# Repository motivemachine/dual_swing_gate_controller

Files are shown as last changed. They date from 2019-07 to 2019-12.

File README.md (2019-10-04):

#### Remote linear actuator controller, for a diy open-source gate opener.

Having built a custom driveway gate and hinge setup I found myself shocked at what a quality dual-swing gate opener costs these days. More importantly, they have rather a lack of customization available in how you control or communicate with them, so I've set out to build my own with a pair of 12v linear actuators and a Semtech SX1287 LORA radio module. This is a work in progress.  

I'll be building a custom PCB for the whole thing, but I've tried to design this in such a way that any number of Arduino and related modules would work if hand-wired with jumpers, perfboard, breadboard, etc. Most parts are through-hole, and the ones that are surface mount are large enough hand soldering should be easy. Also makes for easy customization.

##### Current Status
Schematic and first soldered board is complete. Code testing has begun, and has been mostly reliable with a few adjustments needed in error handling functions and long-term robust-ness. 

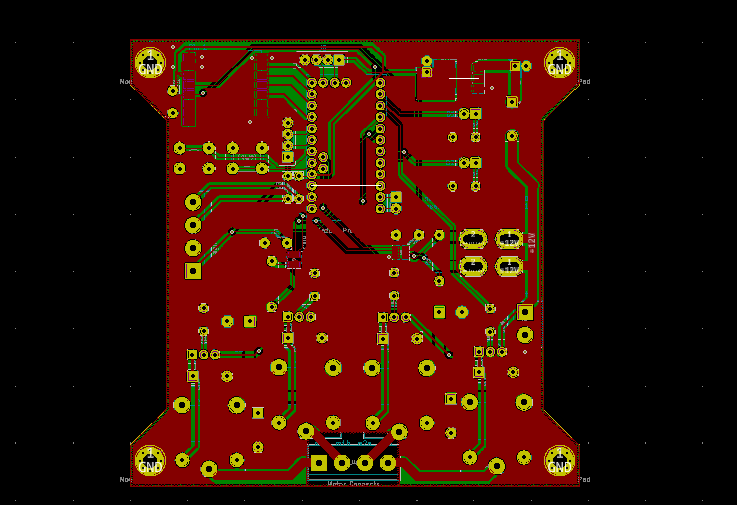
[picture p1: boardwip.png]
gate control board


##### Parts list and design criteria
* **2x 16" stroke linear actuators (12v)** - commercial gate openers are often much larger than this, but so often are the gates larger and heavier. My gates are quite lightweight tubing on ball-bearing hinges, so not much force is needed to open them. The two actuators I have claim a full load current of 3 amps, though I don't expect them to need much more than 1 to open and close these gates
* **2x 8Ah SLA batteries** - the driveway is long enough that trenching AC power out there would be a chore, so I'll be running this off a pair of ~$16 12v batteries and a small solar panel instead.
* **Arduino Pro mini 8Mhz/3.3v** - chosen so that I can avoid level shifting the SPI/I2C modules. An arduino Uno or Nano would work fine with proper level shifting
* **AI-thinker RA-02 Lora** radio - I've come to like these for designs that may be put in varied enclosures, as the IPX connector built-in means I can place the radio anywhere that's convenient and pipe the RF via coax to an optimal antenna placement.
* **4x 12volt SPDT relays** of proper current rating- The relays are in an H-Bridge topology that allows reversing of current through a DC motor(see below). This could be done a little cleaner with a pair of DPDT relays, but using these means the design will also work with the standard 4-place relay modules that are so popular. They are a 12v coil powered off the battery, switched with a PNP from the Atmega328p.
* **2x INA219**- These can be had in SOT23-8 package, or available in several types of breakout boards. These will be the primary safety, which will watch the current going to each actuator. We'll test for a baseline current it usually takes to open a given gate (perhaps in a light breeze) and set that as our upper limit of motor current. If this current is exceeded, it likely means a gate is jammed or attempting to close on an object; so stop and reverse the gate.
  * Most of the pre-built modules I've seen for sale us a 2010 0.1ohm shunt resistor, allowing a maximum current of 3 amps. If your motors draw more than that, recalculate the needed resistor value
  * There will be enough exposed pins to add an electronic-eye, but I haven't planed for that yet.
* **2x mini ATM fuse**- the INA219 will handle over-current due to obstructions in the motor, these are just extra safety in case of a major hardware or wiring failure. Size appropriately to your wire sizes and motor current requirements.
* **AMS1117-3.3 regulator**- For the 3.3v circuitry.
* **A MAG3110 or similar magnetometer**- this is optional, but I've decided to build-in my magnetometer driveway alarm into this same enclosure and power supply. It is described here: [magneto-driveway-alarm](www.gitlab.com/motivemachine/magneto-driveway-alarm)
  * The magnetometer from a more common IMU package (i.e. mpu9250) would likely also work well.

##### H-Bridge description
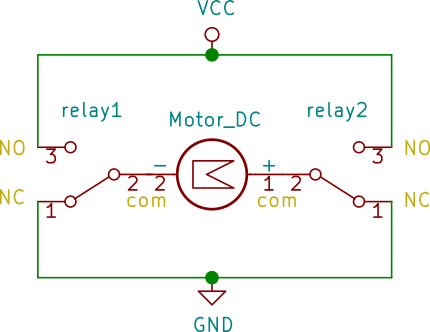
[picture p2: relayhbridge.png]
hbridge schematic
  
Shown here is the relay configuration in a simple H-Bridge. By switching seperate relays, any leg can be made positive, while the other remains grounded, causing the DC motor to be able to turn in two directions. This is very fault tolerant too- if any relay became stuck or failed, the motor would have either both leads grounded, or both leads at 12 volts, neither one of which would allow current to flow, therefore the motor will remain stopped. If the linear actuator is moving, it will of course stop when it reaches the built-in limit switches.
  Avid home DIY'ers might recognize this as similar to wiring a 3-way light switch, but backwards. The other difference is that AC power has no single direction of current flow, nor does a lightbulb care which way the current flows.

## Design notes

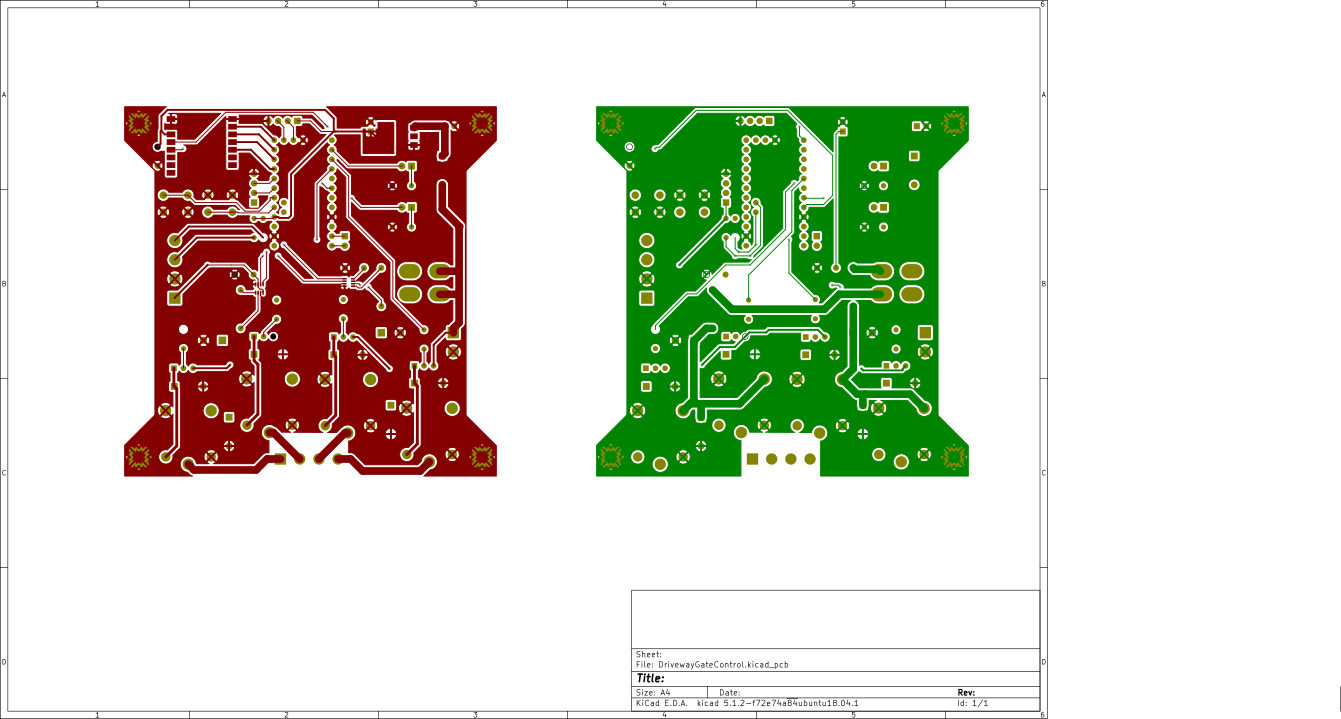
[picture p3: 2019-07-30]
BoardLayers.png

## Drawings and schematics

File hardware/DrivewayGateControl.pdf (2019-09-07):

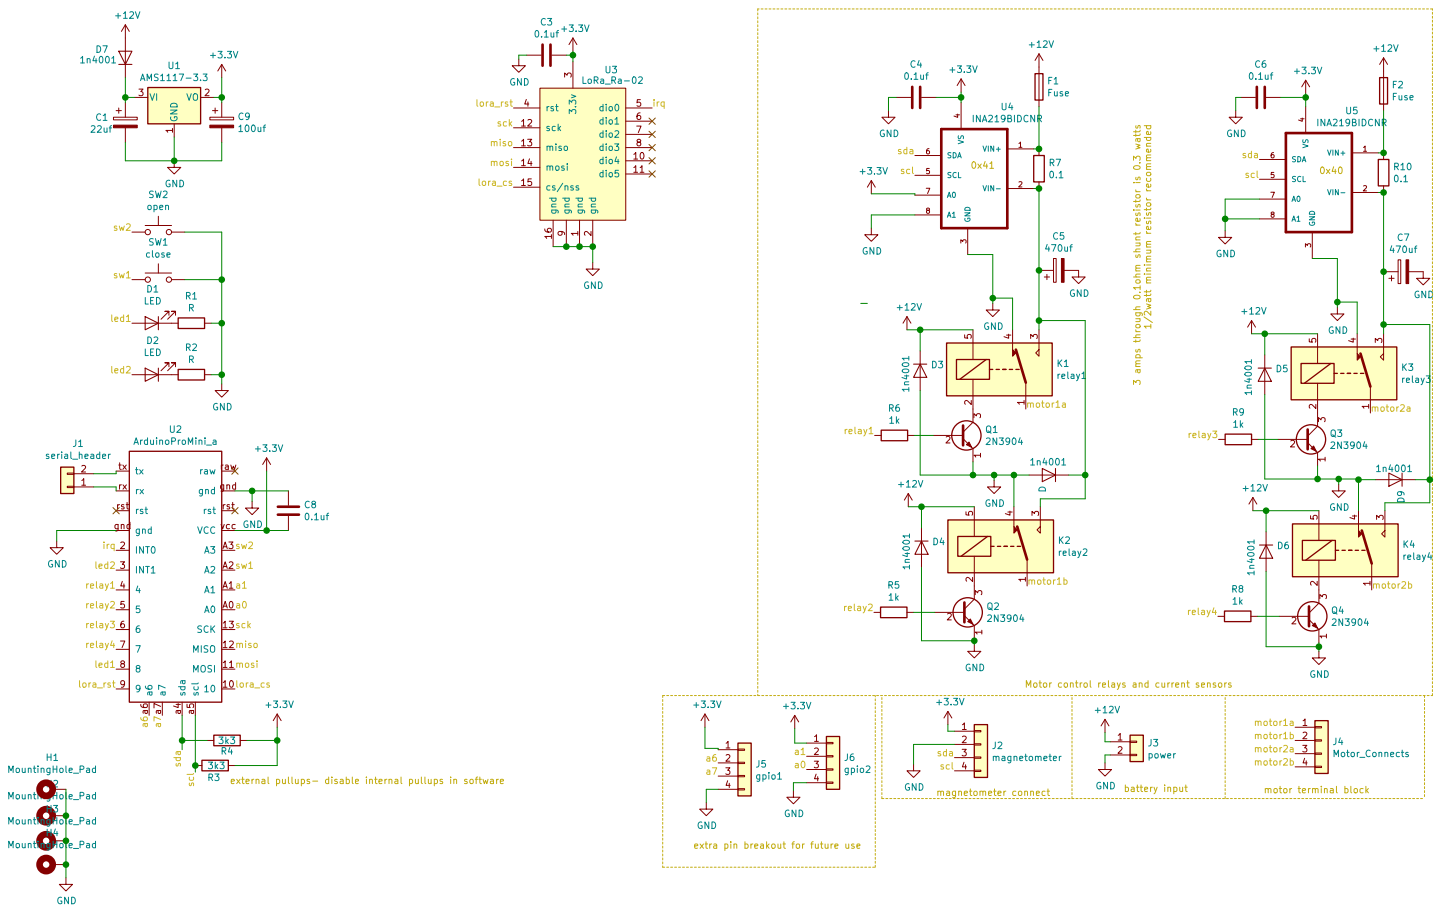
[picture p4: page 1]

external pullups- disable internal pullups in software

extra pin breakout for future use

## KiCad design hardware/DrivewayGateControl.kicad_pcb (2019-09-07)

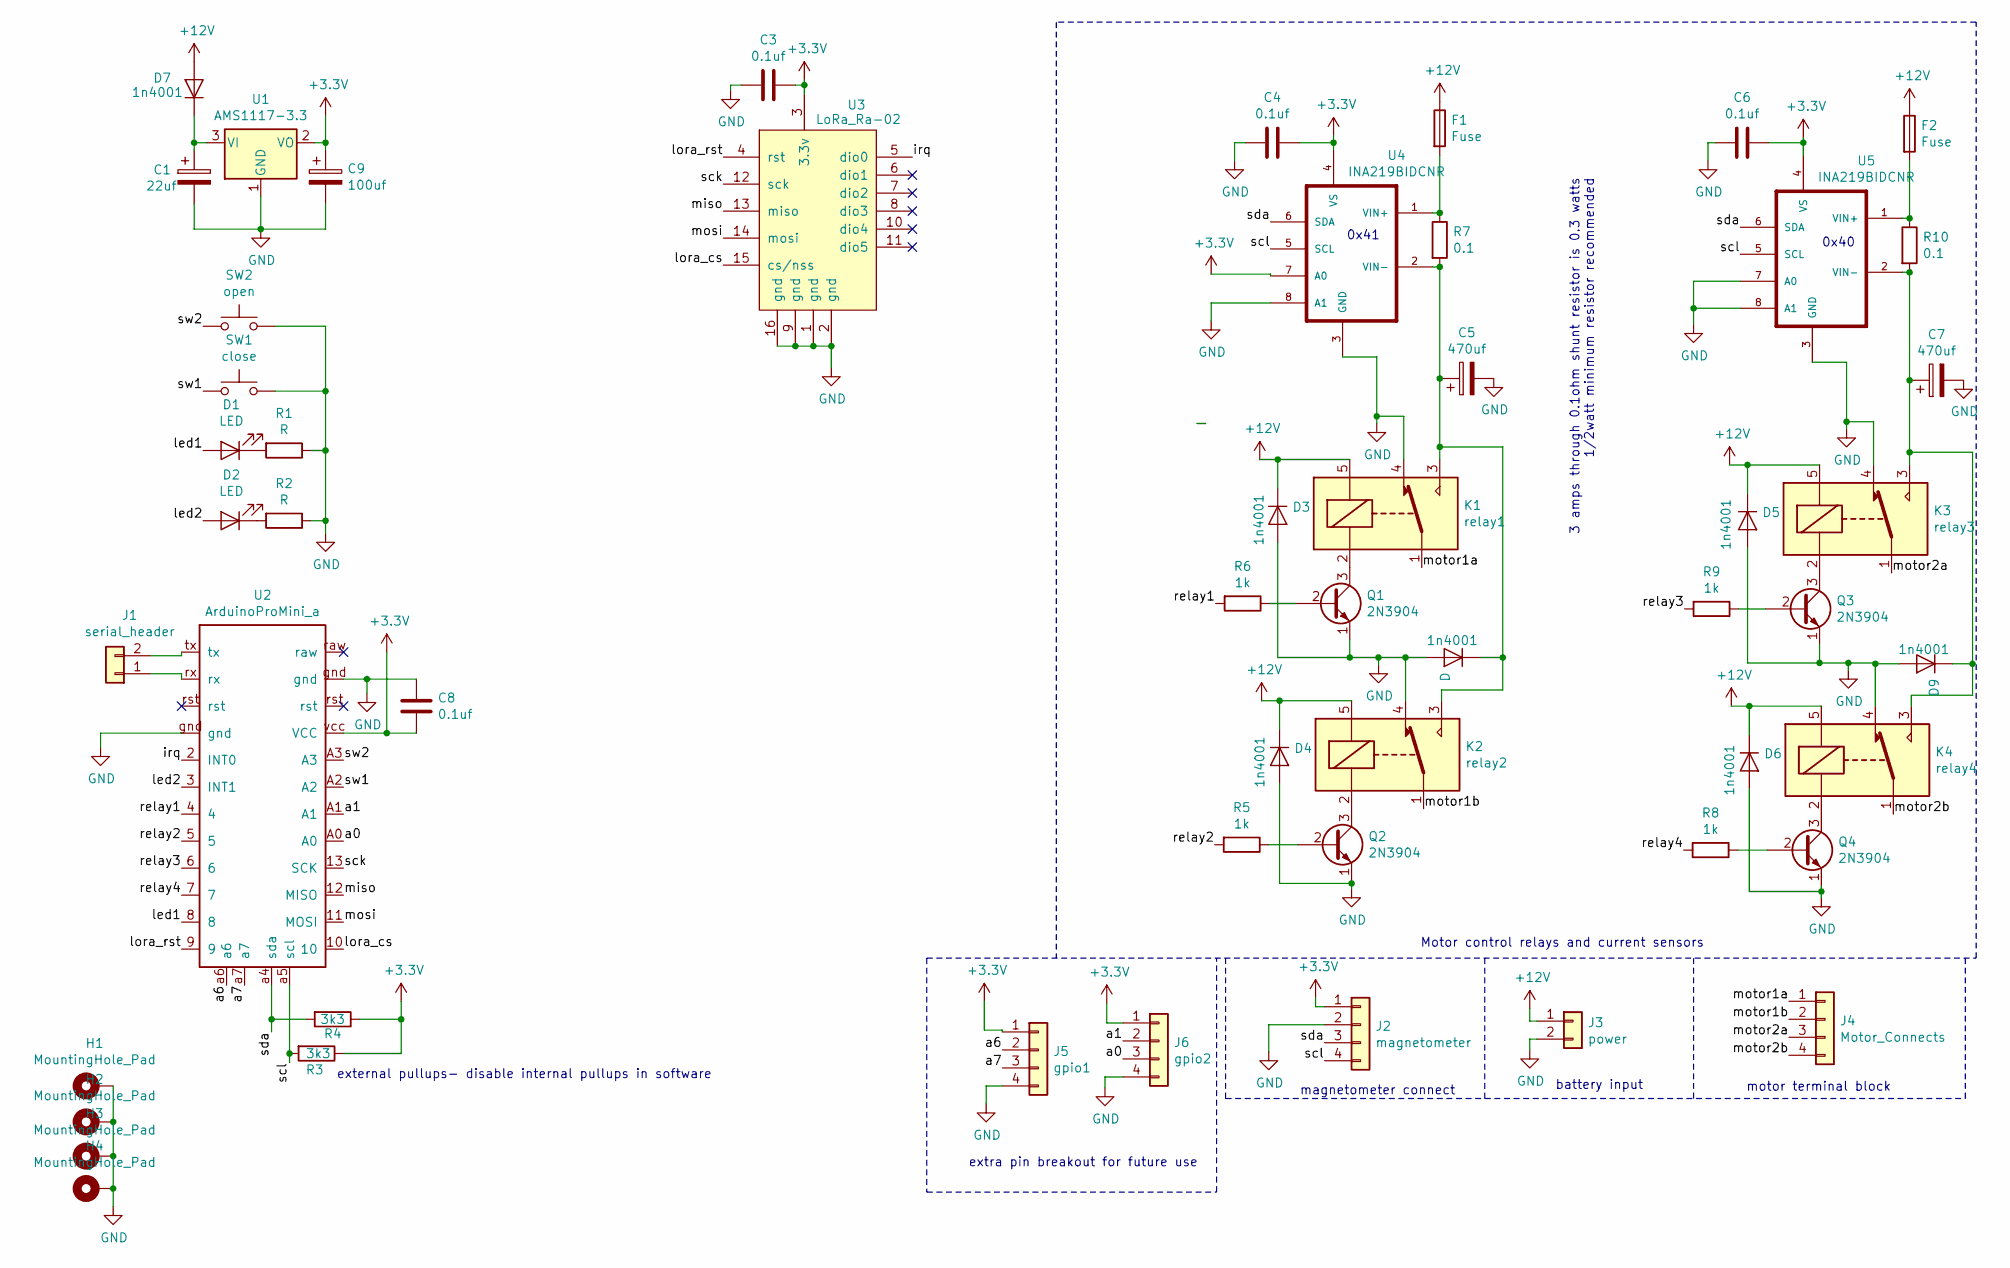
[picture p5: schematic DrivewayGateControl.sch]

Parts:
1n4001: D; D_A-405_P7.62mm_Horizontal
C1: 22uf; CP_Radial_D5.0mm_P2.50mm
C3, C4, C6, C8: 0.1uf; C_Disc_D4.7mm_W2.5mm_P5.00mm
C5, C7: 470uf; CP_Radial_D12.5mm_P5.00mm
C9: 100uf; CP_Radial_D7.5mm_P2.50mm
D1, D2: LED; LED_D5.0mm
D3, D4, D5, D6, D7, D9: 1n4001; D_A-405_P7.62mm_Horizontal
F1, F2: Fuse; Fuse_Blade_Mini_directSolder
H1, H2, H3, H4: MountingHole_Pad; MountingHole_3.2mm_M3_Pad_Via
J1: serial_header; PinHeader_1x02_P2.54mm_Vertical
J2: magnetometer; TerminalBlock_bornier-4_P5.08mm
J3: power; TerminalBlock_bornier-2_P5.08mm
J4: Motor_Connects; TerminalBlock_bornier-4_P5.08mm
J5: gpio1; PinHeader_1x04_P2.54mm_Vertical
J6: gpio2; PinHeader_1x04_P2.54mm_Vertical
K1: relay1; Relay_SPDT_SANYOU_SRD_Series_Form_C
K2: relay2; Relay_SPDT_SANYOU_SRD_Series_Form_C
K3: relay3; Relay_SPDT_SANYOU_SRD_Series_Form_C
K4: relay4; Relay_SPDT_SANYOU_SRD_Series_Form_C
Q1, Q2, Q3, Q4: 2N3904; TO-92_Inline_Wide
R1, R2: R; R_Axial_DIN0207_L6.3mm_D2.5mm_P7.62mm_Horizontal
R3, R4: 3k3; R_Axial_DIN0207_L6.3mm_D2.5mm_P7.62mm_Horizontal
R5, R6, R8, R9: 1k; R_Axial_DIN0207_L6.3mm_D2.5mm_P7.62mm_Horizontal
R7, R10: 0.1; R_Axial_DIN0207_L6.3mm_D2.5mm_P10.16mm_Horizontal
SW1: close; SW_PUSH_6mm_H8.5mm
SW2: open; SW_PUSH_6mm_H8.5mm
U1: AMS1117-3.3; SOT-223-3_TabPin2
U2: ArduinoProMini_a
U3: LoRa_Ra-02; LORA_SX1278_Module
U4, U5: INA219BIDCNR; SOT-23-8

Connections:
+3V3: C3.1, C4.1, C6.1, C8.2, C9.1, J2.1, J5.1, J6.1, R3.1, R4.1, U1.2 (VO), U2.vcc (VCC), U3.3 (3.3v), U4.4 (VS), U4.7 (A0), U5.4 (VS)
+12V: D3.1 (K), D4.1 (K), D5.1 (K), D6.1 (K), D7.2 (A), F1.1, F2.1, J3.1, K1.5, K2.5, K3.5, K4.5
/a0: J6.3, U2.A0
/a1: J6.2, U2.A1
/a6: J5.2, U2.a6
/a7: J5.3, U2.a7
/irq: U2.2 (INT0), U3.5 (dio0)
/led1: D1.2 (A), U2.8
/led2: D2.2 (A), U2.3 (INT1)
/lora_cs: U2.10, U3.15 (cs/nss)
/lora_rst: U2.9, U3.4 (rst)
/miso: U2.12 (MISO), U3.13 (miso)
/mosi: U2.11 (MOSI), U3.14 (mosi)
/motor1a: J4.1, K1.1
/motor1b: J4.2, K2.1
/motor2a: J4.3, K3.1
/motor2b: J4.4, K4.1
/relay1: R6.2, U2.4
/relay2: R5.2, U2.5
/relay3: R9.2, U2.6
/relay4: R8.2, U2.7
/sck: U2.13 (SCK), U3.12 (sck)
/scl: J2.4, R3.2, U2.a5 (scl), U4.5 (SCL), U5.5 (SCL)
/sda: J2.3, R4.2, U2.a4 (sda), U4.6 (SDA), U5.6 (SDA)
/sw1: SW1.1, U2.A2
/sw2: SW2.1, U2.A3
GND: 1n4001.2 (A), C1.2, C3.2, C4.2, C5.2, C6.2, C7.2, C8.1, C9.2, D3.2 (A), D4.2 (A), D5.2 (A), D6.2 (A), D9.2 (A), H1.1, H2.1, H3.1, H4.1, J2.2, J3.2, J5.4, J6.4, K1.4, K2.4, K3.4, K4.4, Q1.1 (E), Q2.1 (E), Q3.1 (E), Q4.1 (E), R1.1, R2.1, SW1.2, SW2.2, U1.1 (GND), U2.gnd, U3.1 (gnd), U3.2 (gnd), U3.9 (gnd), U3.16 (gnd), U4.3 (GND), U4.8 (A1), U5.3 (GND), U5.7 (A0), U5.8 (A1)
unnamed: 1n4001.1 (K), C5.1, K1.3, K2.3, R7.2, U4.2 (VIN-)
unnamed: C1.1, D7.1 (K), U1.3 (VI)
unnamed: C7.1, D9.1 (K), K3.3, K4.3, R10.2, U5.2 (VIN-)
unnamed: D1.1 (K), R1.2
unnamed: D2.1 (K), R2.2
unnamed: F1.2, R7.1, U4.1 (VIN+)
unnamed: F2.2, R10.1, U5.1 (VIN+)
unnamed: J1.1, U2.rx
unnamed: J1.2, U2.tx
unnamed: K1.2, Q1.3 (C)
unnamed: K2.2, Q2.3 (C)
unnamed: K3.2, Q3.3 (C)
unnamed: K4.2, Q4.3 (C)
unnamed: Q1.2 (B), R6.1
unnamed: Q2.2 (B), R5.1
unnamed: Q3.2 (B), R9.1
unnamed: Q4.2 (B), R8.1

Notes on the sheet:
Motor control relays and current sensors
motor terminal block
battery input
magnetometer connect
0x41
0x40
external pullups- disable internal pullups in software
extra pin breakout for future use
3 amps through 0.1ohm shunt resistor is 0.3 watts 1/2watt minimum resistor recommended

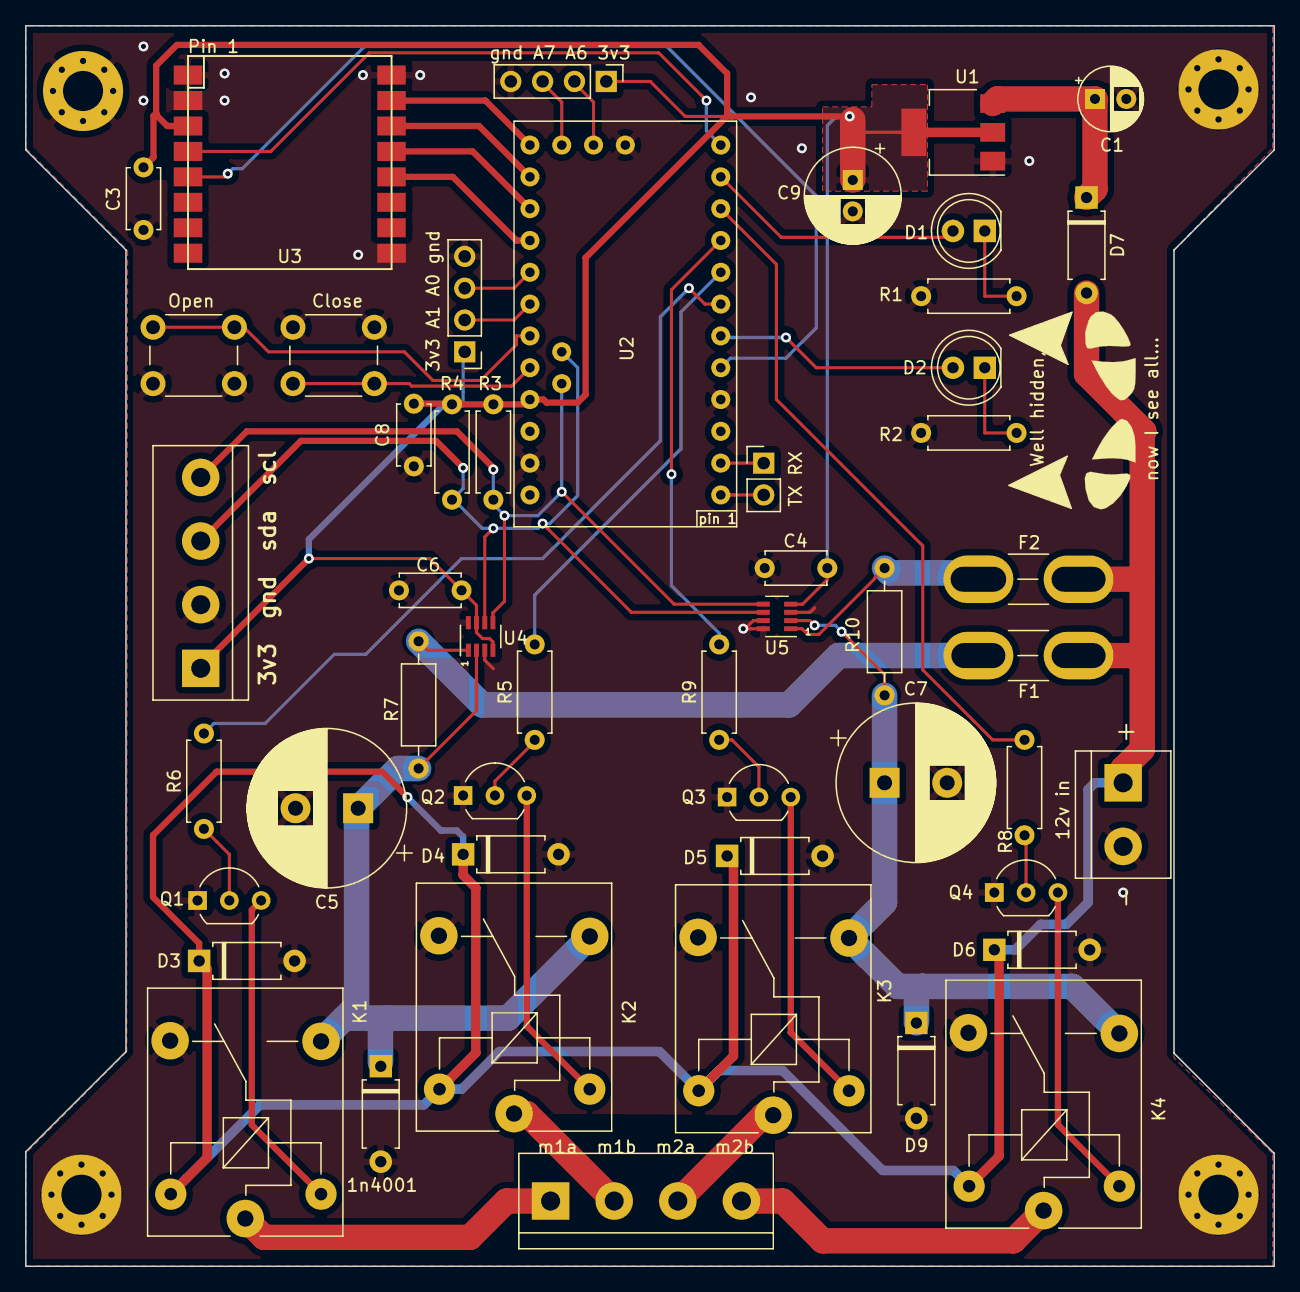
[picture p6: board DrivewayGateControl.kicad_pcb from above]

Board: 2 copper layers, 99.7 x 99.1 mm, 54 parts (0 on the bottom side), 44 nets.

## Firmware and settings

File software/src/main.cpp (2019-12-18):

#include <Arduino.h>
#include <avr/interrupt.h>
#include <SPI.h>
#include <LoRa.h>
#include <EEPROM.h>
#include <Adafruit_INA219.h>
#include <SparkFun_MAG3110.h> //don't forget to make sure the Wire.begin() call in here is for 100khz, not 400khz as is the default from sparkfun

//CHANGES MADE IN THIS VERSION: since installing- turned off heartbeat led, change startup curren limit from 1400ma to 1600, change max current while running from 1000 to 1300ma

#define csPin 10
#define resetPin 9
#define irqPin 2

#define ledOne 8
#define ledTwo 3
#define openbutton A2
#define closebutton A3

#define relayOne 4
#define relayTwo 5
#define relayThree 6
#define relayFour 7

//%%%%%%%%%%%%%%%%%%% TODO %%%%%%%%%%%%%%%%%%%%%%%
//more serial debug

MAG3110 mag = MAG3110(); //magnetometer setup
int deviation = 15;  // starting at 15 for the new sensor
int16_t x,y,z;
int oldx,oldy,oldz;
int const bufferLen = 8;
int msgid = 0;

int xbuffer[bufferLen]; // initalize circular buffer for XYZ averaging of reads.
int ybuffer[bufferLen];
int zbuffer[bufferLen];
int xaverage;
int yaverage;
int zaverage;
const String alarm_msg = "DRV";
unsigned long alarm_active = 0;
unsigned long last_checkin = 0;
unsigned long last_battery_check = 0;
unsigned long checkin_delay = 14000000;
unsigned int alarm_delay = 5000;

Adafruit_INA219 inaOne(0x40);    //INA219 current sensor constructors
Adafruit_INA219 inaTwo(0x41);

float busvoltageOne = 0; //only need to know battery voltage from one sensor
float shuntvoltageOne = 0;
float loadvoltageOne = 0; //calculated from bus and shunt voltage in function getLoadVoltage()
float busvoltageTwo = 0;
float shuntvoltageTwo = 0;
float loadvoltageTwo = 0;
float currentMaOne = 0; //setting up current readings
float currentMaTwo = 0;
float maxcurrent = 1300.0; //maximum allowable current. Should be set to just slightly higher than what is required to open the gate. Any higher value is assumed to be cause by a jammed motor or gate pressing on an obstacle. Is in milliamps

byte localAddress = 0x13; //19
byte destAddress = 0x25; //37
bool packetToParse = false;

unsigned long runtime = 32000; //slightly longer than the motors should stay to to fully open/close. 16" acutators take about 28 seconds from limit to limit, plus some delays to stagger the startup current
bool open[4] = {1,0,1,0}; //relay states for opening/retracting both actuators
bool close[4] = {0,1,0,1};
bool closeflag = false; // flag to determine if the gate is supposed to close or not
bool openflag = false; // flag to determine if the gate is supposed to open or not
bool gateisopen = false; // system needs to start with gate open [actuators retracted]. answers the question 'is the gate open'


void getLoadVoltage() // returns nothing, just update global variables.
  {
    busvoltageOne = inaOne.getBusVoltage_V();
    shuntvoltageOne = inaOne.getShuntVoltage_mV();
    loadvoltageOne = busvoltageOne + (shuntvoltageOne / 1000);
    busvoltageTwo = inaTwo.getBusVoltage_V();
    shuntvoltageTwo = inaTwo.getShuntVoltage_mV();
    loadvoltageTwo = busvoltageTwo + (shuntvoltageTwo / 1000);
  }

void faultmessage(String faultType) //called when experiencing fault. "fault1" = no bus voltage , "fault2" = no bus current , "fault3" = overcurrent
  {
    delay(100);
    LoRa.beginPacket();
    LoRa.write(destAddress);
    LoRa.write(localAddress);
    LoRa.write(msgid);
    LoRa.write(faultType.length());
    LoRa.print(faultType);
    LoRa.endPacket();
    msgid++;
    delay(100);
    LoRa.receive();
  }

void checkin()
{
    String const online PROGMEM = "Gate sentry online";
    delay(200);
    LoRa.beginPacket();
    LoRa.write(destAddress);
    LoRa.write(localAddress);
    LoRa.write(11); // message ID,
    LoRa.write(online.length());
    LoRa.print(online);
    LoRa.endPacket();
    msgid++;
    delay(100);
    LoRa.receive();
}

void openGate()
{
  unsigned long currentTime = millis(); //when the motors started running
  if (gateisopen == true)
  { // gate is already open
    //Serial.println("already open");
    openflag = false;
    closeflag = false;
    gateisopen = false;
    return;
  }
  bool errorFlag = false;
  //Serial.println(F("Retracting actuators"));
  digitalWrite(relayOne, open[0]);  //opening gate, retracting actuators
  digitalWrite(relayTwo, open[1]);
  delay(200); //slightly offset startup current by not starting motors at exact same time
  digitalWrite(relayThree, open[2]);
  digitalWrite(relayFour, open[3]);
  delay(1000); //short delay for motors to spin up?
  getLoadVoltage();
  currentMaOne = inaOne.getCurrent_mA();
  currentMaTwo = inaTwo.getCurrent_mA();
  delay(10);
  //Serial.print("current ma:"); Serial.println(currentMaOne);
  //Serial.print("current ma:"); Serial.println(currentMaTwo);
  if (loadvoltageOne < 6 || loadvoltageTwo < 6) //no voltage on actuator lines mean blown fuses
  {
    digitalWrite(relayOne, LOW);
    digitalWrite(relayTwo, LOW);
    delay(100);
    digitalWrite(relayThree, LOW);
    digitalWrite(relayFour, LOW);
    //Serial.println("no volt fault");
    faultmessage("fault1");
    openflag = false; //setitng these equal to false will 'zero out' the flags if any change occured due to an interrupt for the radio setting one to true. Prevents opener from acting on multiple open/close commands recieved while the gate is in motion
    closeflag = false;
    gateisopen = true;
    return;
  }
  else if (currentMaOne < 100 || currentMaTwo < 100) //no current on actuator lines means motor disconnected
  {
    digitalWrite(relayOne, LOW);
    digitalWrite(relayTwo, LOW);
    delay(100);
    digitalWrite(relayThree, LOW);
    digitalWrite(relayFour, LOW);
    //Serial.println("no crnt fault");
    faultmessage("fault2");
    openflag = false; //setitng these equal to false will 'zero out' the flags if any change occured due to an interrupt for the radio setting one to true. Prevents opener from acting on multiple open/close commands recieved while the gate is in motion
    closeflag = false;
    gateisopen = true;
    return;
  }
  else if (currentMaOne > 1600 || currentMaTwo > 1600) //overcurrent as soon as things are moving means something is very jammed. Just stop all motors.
  {
    digitalWrite(relayOne, LOW);
    digitalWrite(relayTwo, LOW);
    delay(100);
    digitalWrite(relayThree, LOW);
    digitalWrite(relayFour, LOW);
    //Serial.println("overcurrent");
    faultmessage("fault3");
    openflag = false; //setitng these equal to false will 'zero out' the flags if any change occured due to an interrupt for the radio setting one to true. Prevents opener from acting on multiple open/close commands recieved while the gate is in motion
    closeflag = false;
    //gateisopen = false;
    return;
  }
  while (millis() - currentTime < runtime)
  {
    currentMaOne = inaOne.getCurrent_mA();
    currentMaTwo = inaTwo.getCurrent_mA();
    //Serial.print("crnt 1: "); Serial.println(currentMaOne);
    //Serial.print("crnt 2: "); Serial.println(currentMaTwo);
    if (currentMaOne > maxcurrent ||currentMaTwo > maxcurrent) // if max current exceeded, stop motors, pause, move if opposite direction and stop.
    {
        currentTime += 2500; // add 2.5 seconds to compensate for delays on stopping and reversing. Will run until actuators are fullly open
        //Serial.println("overcurrent");
        digitalWrite(relayOne, LOW);
        digitalWrite(relayTwo, LOW);
        delay(200);
        digitalWrite(relayThree, LOW);
        digitalWrite(relayFour, LOW);
        delay(1500);
        digitalWrite(relayOne, close[0]);
        digitalWrite(relayTwo, close[1]);
        delay(200); //slightly offset startup current by not starting motors at exact same time
        digitalWrite(relayThree, close[2]);
        digitalWrite(relayFour, close[3]);
        delay(100);
        faultmessage("fault3");
        errorFlag = true;

        // if (currentMaOne > maxcurrent || currentMaTwo > maxcurrent) // if max current exceeded while reversing direction, just stop everything and wait.
        // {
        //   Serial.println("double overcurrent");
        //   digitalWrite(relayOne, LOW);
        //   digitalWrite(relayTwo, LOW);
        //   delay(200);
        //   digitalWrite(relayThree, LOW);
        //   digitalWrite(relayFour, LOW);
        //   delay(200);
        // }
      //}
      // digitalWrite(relayOne, LOW);
      // digitalWrite(relayTwo, LOW);
      // delay(200);
      // digitalWrite(relayThree, LOW);
      // digitalWrite(relayFour, LOW);
    }
    delay(500); // pause before rereading current
  }
  digitalWrite(relayOne, LOW);
  digitalWrite(relayTwo, LOW);
  delay(100);
  digitalWrite(relayThree, LOW);
  digitalWrite(relayFour, LOW);
  openflag = false; //setitng these equal to false will 'zero out' the flags if any change occured due to an interrupt for the radio setting one to true. Prevents opener from acting on multiple open/close commands recieved while the gate is in motion
  closeflag = false;
  gateisopen = true;
  if (errorFlag == true) gateisopen = false; //if gate reversed, it's closed now, not opener
  errorFlag = false;
  LoRa.receive();
}

void closeGate()
{
  unsigned long currentTime = millis(); //when the motors started running
  if (gateisopen == false)
  { // gate is already closed
    //Serial.println("already closed");
    closeflag = false;
    openflag = false;
    gateisopen = true; // set to true so that if control was started with gate in wrong position, is will reset and try to open on second try.
    return;
  }
  bool errorFlag = false;
  //Serial.println(F("Extending actuators"));
  digitalWrite(relayOne, close[0]);  //closing gate, extending acutators
  digitalWrite(relayTwo, close[1]);
  delay(200); //slightly offset startup current by not starting motors at exact same time
  digitalWrite(relayThree, close[2]);
  digitalWrite(relayFour, close[3]);
  delay(1000); //short delay for motors to spin up?
  getLoadVoltage();
  currentMaOne = inaOne.getCurrent_mA();
  currentMaTwo = inaTwo.getCurrent_mA();
  delay(10);
  //Serial.print("current ma:"); Serial.println(currentMaOne);
  //Serial.print("current ma:"); Serial.println(currentMaTwo);
  if (loadvoltageOne < 6 || loadvoltageTwo < 6) //no voltage on actuator lines mean blown fuses
  {
    digitalWrite(relayOne, LOW);
    digitalWrite(relayTwo, LOW);
    delay(100);
    digitalWrite(relayThree, LOW);
    digitalWrite(relayFour, LOW);
    faultmessage("fault1");
    //Serial.println("no volt fault");
    closeflag = false; //setitng all these equal to false will 'zero out' the flags if any change occured due to an interrupt for the radio setting one to true. Prevents opener from acting on multiple open/close commands recieved while the gate is in motion
    openflag = false;
    gateisopen = false;
    return;
  }
  else if (currentMaOne < 100 || currentMaTwo < 100) //no current on actuator lines means motor disconnected
  {
    digitalWrite(relayOne, LOW);
    digitalWrite(relayTwo, LOW);
    delay(100);
    digitalWrite(relayThree, LOW);
    digitalWrite(relayFour, LOW);
    faultmessage("fault2");
    //Serial.println("no crnt fault");
    closeflag = false; //setitng all these equal to false will 'zero out' the flags if any change occured due to an interrupt for the radio setting one to true. Prevents opener from acting on multiple open/close commands recieved while the gate is in motion
    openflag = false;
    //gateisopen = false;
    return;
  }
  else if (currentMaOne > 1400 || currentMaTwo > 1400) //overcurrent as soon as things are moving means something is very jammed. Just stop all motors.
  {
    //Serial.println("overcurrent");
    digitalWrite(relayOne, LOW);
    digitalWrite(relayTwo, LOW);
    delay(100);
    digitalWrite(relayThree, LOW);
    digitalWrite(relayFour, LOW);
    faultmessage("fault3");
    closeflag = false; //setitng all these equal to false will 'zero out' the flags if any change occured due to an interrupt for the radio setting one to true. Prevents opener from acting on multiple open/close commands recieved while the gate is in motion
    openflag = false;
    gateisopen = false;
    return;
  }
  while (millis() - currentTime < runtime) // run motors for 30 seconds, checking every 400ms for a motor overcurrent condition
  {
    currentMaOne = inaOne.getCurrent_mA();
    currentMaTwo = inaTwo.getCurrent_mA();
    //Serial.print("crnt 1: "); Serial.println(currentMaOne);
    //Serial.print("crnt 2: "); Serial.println(currentMaTwo);
    if (currentMaOne > maxcurrent || currentMaTwo > maxcurrent) // if max current exceeded, stop motors, pause, move in opposite direction and stop.
    {
        currentTime += 2500; // add 2.5 seconds to currentTime to compenstate for stop/reverse delays
        //Serial.println("overcurrent");
        digitalWrite(relayOne, LOW);
        digitalWrite(relayTwo, LOW);
        delay(200);
        digitalWrite(relayThree, LOW);
        digitalWrite(relayFour, LOW);
        delay(1500);
        digitalWrite(relayOne, open[0]);
        digitalWrite(relayTwo, open[1]);
        delay(200); //slightly offset startup current by not starting motors at exact same time
        digitalWrite(relayThree, open[2]);
        digitalWrite(relayFour, open[3]);
        delay(100);
        faultmessage("fault3");
        errorFlag = true;
      //   currentMaOne = inaOne.getCurrent_mA();
      //   currentMaTwo = inaTwo.getCurrent_mA();
        // if (currentMaOne > maxcurrent || currentMaTwo > maxcurrent) // if max current exceeded while reversing direction, just stop everything and halt until reset.
        // {
        //   Serial.println("double overcurrent");
        //   digitalWrite(relayOne, LOW);
        //   digitalWrite(relayTwo, LOW);
        //   delay(200);
        //   digitalWrite(relayThree, LOW);
        //   digitalWrite(relayFour, LOW);
        //   delay(250);
        // }
      //}
      // digitalWrite(relayOne, LOW);
      // digitalWrite(relayTwo, LOW);
      // delay(200);
      // digitalWrite(relayThree, LOW);
      // digitalWrite(relayFour, LOW);
    }
    delay(500); // pause before rereading current
  }
  digitalWrite(relayOne, LOW);
  digitalWrite(relayTwo, LOW);
  delay(200);
  digitalWrite(relayThree, LOW);
  digitalWrite(relayFour, LOW);
  closeflag = false; //setitng all these equal to false will 'zero out' the flags if any change occured due to an interrupt for the radio setting one to true. Prevents opener from acting on multiple open/close commands recieved while the gate is in motion
  openflag = false;
  gateisopen = false;
  if (errorFlag == true) gateisopen = true; //if gate reversed, it's open now, not closed
  errorFlag = false;
  LoRa.receive();
}

// void packetReceived(int packetSize) //ISR to set flag for parsing a packet.
// {
//   packetToParse = true;
// }

void receiving(int packetSize) // crap, is this an interrupt function?
{
  if (packetSize == 0) return;
  int i = 0;
  int recipient = LoRa.read();
  if (recipient != localAddress) return; //message isn't for us, quit parsing
  byte sender = LoRa.read();
  //Serial.print("sndr: "); Serial.println(sender);
  byte incomingMsgId = LoRa.read();
  byte incomingLength = LoRa.read();

  char incomingArray[incomingLength];
  while (LoRa.available())
  {
    incomingArray[i] = (char)LoRa.read();
    i++;
  }
  // Serial.print("incomingArray = "); Serial.write(incomingArray, incomingLength);Serial.print(" : "); Serial.println(incomingLength);
  // Serial.println(strlen(incomingArray));
  // Serial.println(strncmp(incomingArray, "OPEN",4));
  // Serial.println(strncmp(incomingArray, "CLOSE",5));
  // Serial.println(strncmp(incomingArray, "STAT",4));
  if (strncmp(incomingArray,"OPEN",4) == 0) // strcmp never works right. maybe there's a trailing newline issue? strncmp and defining the expected array length seems to work fine
  {
    //Serial.println("open req");
    openflag = true;
    closeflag = false;
  }
  else if (strncmp(incomingArray,"CLOSE",5) == 0)
  {
    //Serial.println("close req");
    closeflag = true;
    openflag = false;
  }
  else if (strncmp(incomingArray,"TOG",3) == 0)
  {
    if (gateisopen == true)
    {
      closeflag = true;
      openflag = false;
    }
    else
    {
      closeflag = false;
      openflag = true;
    }
  }
  else if (strncmp(incomingArray,"STAT",4) == 0)
  {
    //Serial.println("status req");
    checkin();
  }
  //else
  //{
    //Serial.println("rx unrec");
  //}
    // if (openflag)
    // {
    //   // put lora status message ehre
    // }
    // else if (closeflag)
    // {
    //   // put lora status message here
    // }
  //there will be some ack/nack and collision detection, eventually
  // else if ((char*)incomingArray == "ACK")
  //   {
  //     needAck = false;
  //   }
  //  attachInterrupt(uint8_t, void (*)(), int mode)
}


void getgauss(){ //driveway magnetometer alarm reading
  xaverage = 0;
  yaverage = 0;
  zaverage = 0;
  int tempxaverage = 0; // temporary storage for the maths
  int tempyaverage = 0;
  int tempzaverage = 0;
  for (int i; i<=bufferLen; i++)
  {
    if(mag.dataReady())
    {
      mag.readMag(&x, &y, &z);
    }
    xbuffer[i] = x; // add new readings to buffer
    ybuffer[i] = y;
    zbuffer[i] = z;
    delay(30);    //lets try 8 reads every 1/2 second
  }
  for (int t; t<=bufferLen; t++)   //average everything into a single number for x, y, z
  {
    xaverage = xbuffer[t] + xaverage;
    yaverage = ybuffer[t] + yaverage;
    zaverage = zbuffer[t] + zaverage;
  }
    tempxaverage = xaverage/bufferLen;
    tempyaverage = yaverage/bufferLen;
    tempzaverage = zaverage/bufferLen;

    xaverage = abs(tempxaverage); //absolute value taken to measure difference from last reading, positive or negative is not important for our use
    yaverage = abs(tempyaverage);
    zaverage = abs(tempzaverage);
    //just printing the numbers to watch for changes while testing with magnet near sensor
    //Serial.print("Averages: "); Serial.print(xaverage); Serial.print(" "); Serial.print(yaverage); Serial.print(" "); Serial.println(zaverage);
}

void alarmmessage()
{
  //Serial.println("sending");
  delay(200);
  LoRa.beginPacket();
  LoRa.write(destAddress);
  LoRa.write(localAddress);
  LoRa.write(msgid); // message ID, incremented by one at every alarm
  LoRa.write(alarm_msg.length());
  LoRa.print(alarm_msg);
  LoRa.endPacket();
  msgid++;
}

void batteryCheck()
{
  //send low battery alert
  getLoadVoltage();
  if (loadvoltageOne < 12 && loadvoltageTwo <12)
    {
      LoRa.beginPacket();
      LoRa.write(destAddress);
      LoRa.write(localAddress);
      LoRa.write(msgid); // message ID, incremented by one at every alarm
      LoRa.write(4);
      LoRa.print("batt");
      LoRa.endPacket();
      msgid++;
      delay(100);
      LoRa.receive();
    }
  last_battery_check = millis();
}
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
void loop()
{
  //digitalWrite(ledOne, HIGH); // heartbeat blink for testing. will remove later
  delay(250);
  //check magnetometer readings every second, and check timers and battery voltage.
  //incoming radio messages are handled by an ISR that sets

  // getgauss();
  // if (((xaverage-oldx > deviation) || (yaverage-oldy > deviation) || (zaverage-oldz > deviation)))
  // {
  //   Serial.println("magnetic alarm");
  //   alarm_active = millis(); // reset alarm delay, to prevent constant triggering from the same slow vehicle
  //   alarmmessage();
  //   //LoRa.sleep();
  //   delay(alarm_delay); // delay before re-reading the sensor and re-zeroing magnetometer values. This will allow time for the vehicle to pass or stop near the sensor. The alarm will not continuously trip if the vehicle remains in range of the sensor. The alarm WILL trip when the vehicle moves again.
  //   getgauss();
  //   oldx = xaverage;
  //   oldy = yaverage;
  //   oldz = zaverage;
  // }
  if (millis() - last_checkin > checkin_delay) //
  {
    //Serial.println("check in");
    checkin();
    last_checkin = millis();
  }
  if (openflag == true)
  {
    openGate();
  }
  if (closeflag == true)
  {
    closeGate();
  }
  if (millis() - last_battery_check > 600000) //check battery level every 10 minutes
  {
    //Serial.println("battery check");
    batteryCheck();
  }
  if (digitalRead(openbutton) == LOW)
   {
     openflag = true; //override flags to attempt opening or closing when button is pushed
     gateisopen = false;
     openGate();
   }
  if (digitalRead(closebutton) == LOW)
  {
    closeflag = true; //override flags to attempt opening or closing when button is pushed
    gateisopen = true;
    closeGate();
  }
  //digitalWrite(ledOne, LOW);
  delay(250); //delay for led blink
}

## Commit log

2019-07-03 upload design files
    [DrivewayGateControl.kicad_pcb, DrivewayGateControl.sch]
2019-07-06 fixed wildly wrong shunt resistor value
    [DrivewayGateControl.sch]
2019-07-30 update silkscreen, add more pin breakouts
    [DrivewayGateControl.kicad_pcb, DrivewayGateControl.sch]
2019-09-07 fixed relay switch issue
    [DrivewayGateControl.kicad_pcb, DrivewayGateControl.sch]
2019-10-04 fix serial glitch and adjust error functions
    [main.cpp]
2019-12-18 tweaked current limits
